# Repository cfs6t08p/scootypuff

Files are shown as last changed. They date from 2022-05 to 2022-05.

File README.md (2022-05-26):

# BOM

## OTC parts
- 1x NEMA34 stepper motor of your choice
- 1x 400mm linear rail with MGN12H carriage
- 1x Stepper motor driver ..and a way to control it TBA, in the meantime OSSM controller might work?

## 3D printed parts
- 1x Baseplate
- 1x Bearing holder
- 1x Bearing spacer (print in TPU for best fit)
- 1x Enclosure
- 1x Pinion for 14mm shaft with keyway
- 1x Rack (prints in 2 pieces)
- 1x 24mm rail thread mount
- 1x 24mm toy mount to taste

## Hardware
### Rail & attachments
- 12x 2.5x12mm wood screws
- 4x M3x12mm bolts
- 6x M3 lock nuts
- 4x M3x20mm machine screws
- 1x 5x80mm wood screw (for the Vac-u-lock adapter)

### Motor assembly
- 4x M5x30mm bolts
- 4x M5 lock nuts
- 2x M6x80mm bolts
- 2x M6 lock nuts

# How to assemble

1. Fit M3x12mm bolts with double lock nuts into the 3rd mounting hole from one side of the rail, as well as the very last mounting hole on the other side, these will act as hard stops to prevent the rail from leaving the bearing carriage
2. Attach the 24mm rail thread mount to the last two mounting holes on the end of the linear rail with two M3x12mm bolts
3. Attach the two rack pieces to the rail with 2.5x12mm wood screws, the two pieces should fit end to end, run the pinion across before tightening to ensure proper alignment
4. Mount the linear rail carriage to the bearing holder + bearing spacer with four M3x20mm machine screws, use loctite to prevent the screws from loosening with vibration
5. Mount the base plate to the front face of the motor using only two M5x30mm bolts on the bearing side, the bolts on the other side will be fitted after the enclosure is on
6. Mate the pinion to the motor shaft, the top of the pinion should be flush with the top of the shaft
7. Place the bottom part of the bearing holder into its final position on the base plate, then attach the enclosure to the top side, the parts should loosely stay in place without fastening
8. This is the perfect time to make sure the controller is working as expected, beyond this step there may be damage to the machine if the rail is driven past its limits
9. Fit the M6x80mm bolts through the top of the enclosure, the bearing holder and the baseplate
10. Fit the remaining two M5x30mm bolts through the enclosure, the base plate and the front face of the motor
11. If using the Vac-u-lock adapter, run the 5x80mm wood screw through the hole in the bottom, do not be tempted to skip this step, the plastic will crack even with moderate use!
12. This machine is incredibly powerful, be safe and make sure it can be switched off immediately if there is a problem
13. Enjoy!

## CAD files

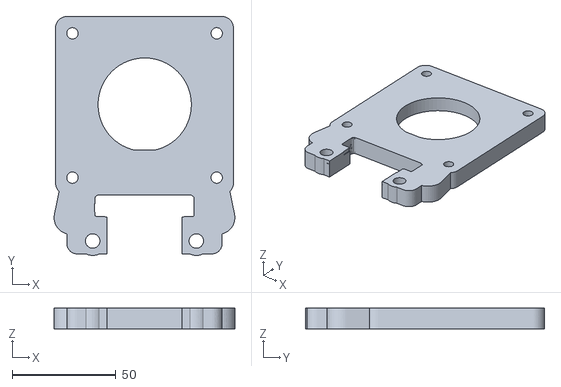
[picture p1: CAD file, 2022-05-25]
baseplate.stl
87.2 x 115.3 x 10.00

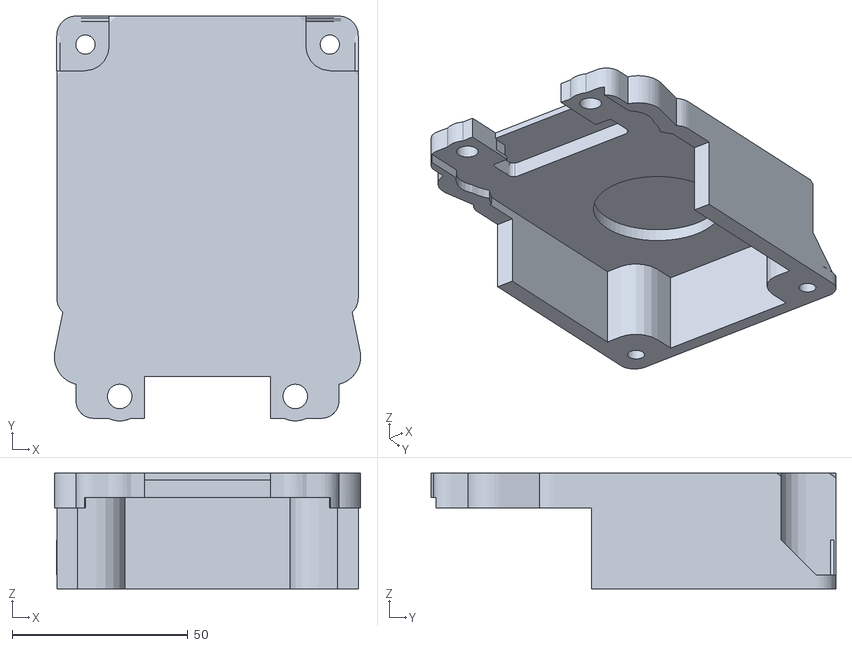
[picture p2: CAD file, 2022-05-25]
enclosure.stl
87.2 x 115.3 x 33.0

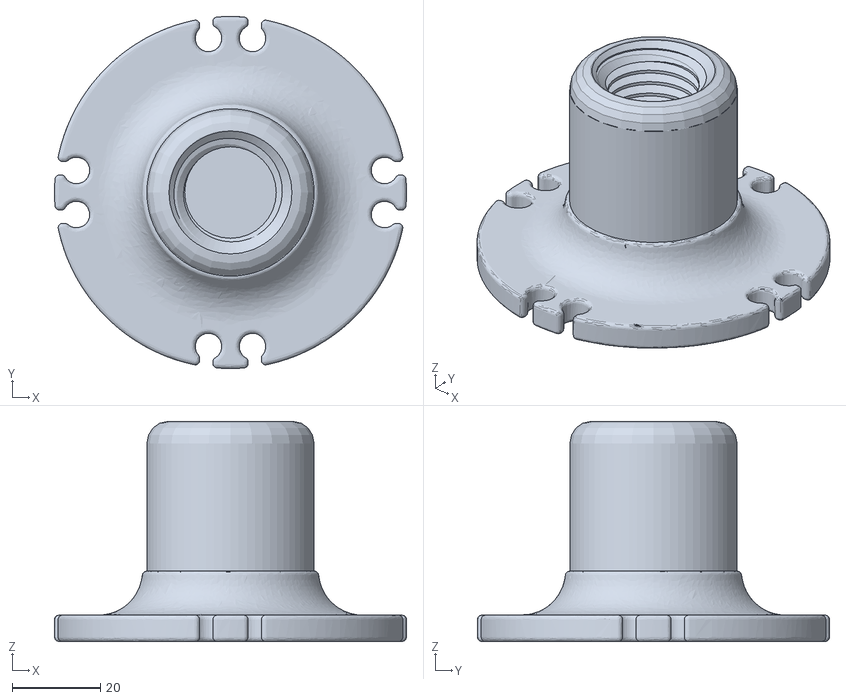
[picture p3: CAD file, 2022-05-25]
OSSM Platten - threaded 50mm.stl
80.0 x 80.0 x 50.0

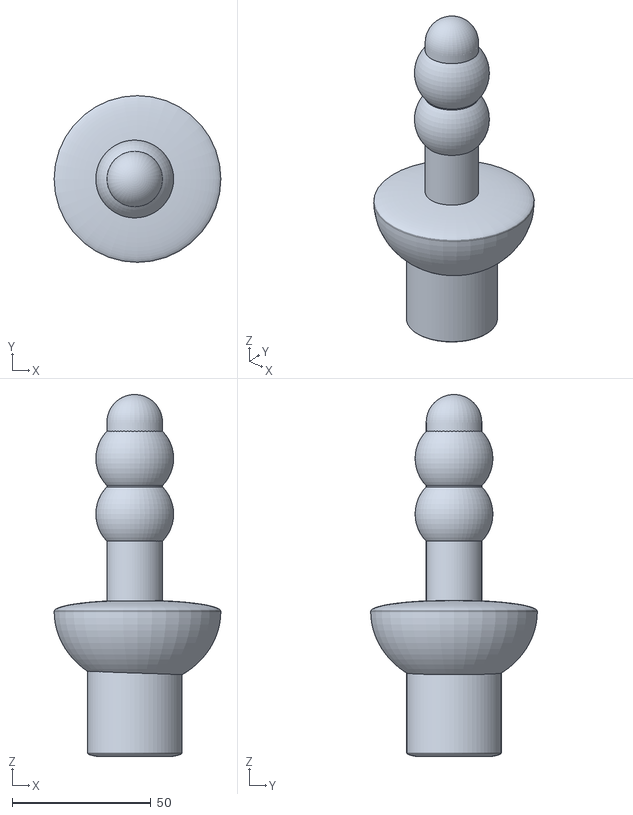
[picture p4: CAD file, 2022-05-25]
Toy mount 24mm threaded plate.stl
60.0 x 60.0 x 130.2

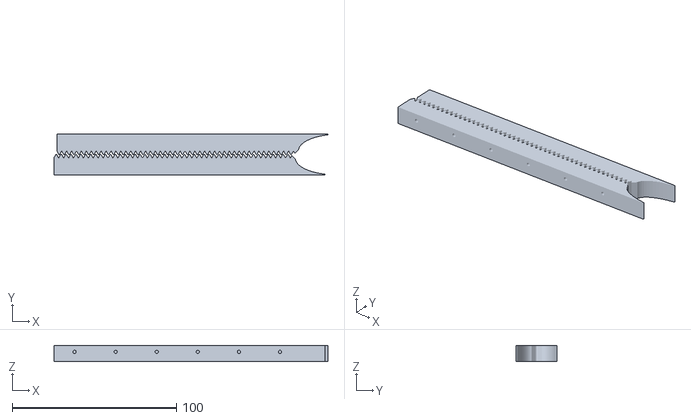
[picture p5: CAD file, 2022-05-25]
Rack_55T_pair_3mmx10x12.5.stl
166.7 x 24.8 x 10.0

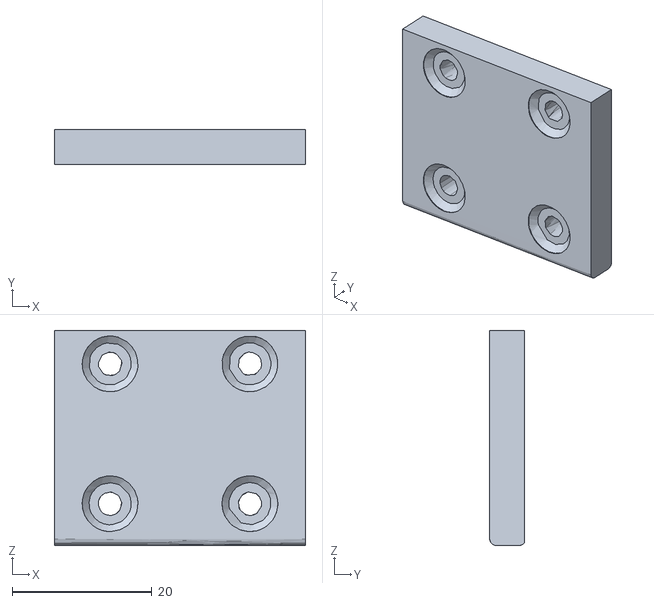
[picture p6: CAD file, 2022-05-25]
flat_bearing_spacer.stl
35.9 x 5.00 x 30.8

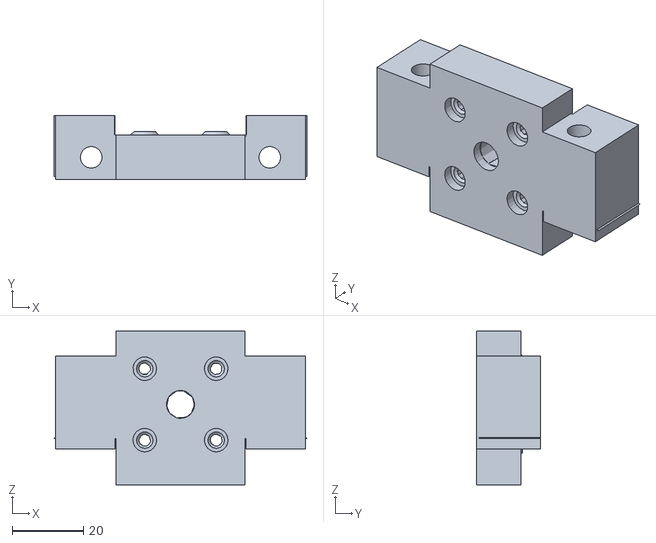
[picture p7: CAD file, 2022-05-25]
bearingholder.stl
70.8 x 17.8 x 43.0

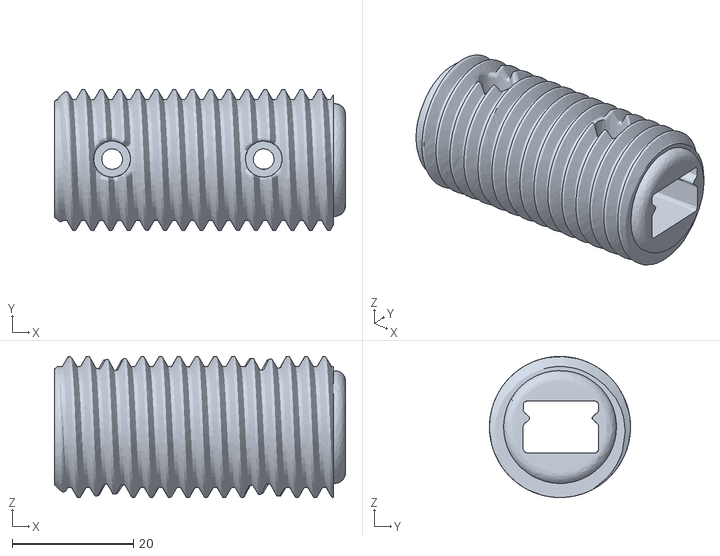
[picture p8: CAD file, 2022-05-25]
OSSM 24mm rail Thread mount M3.stl
48.0 x 23.3 x 23.3

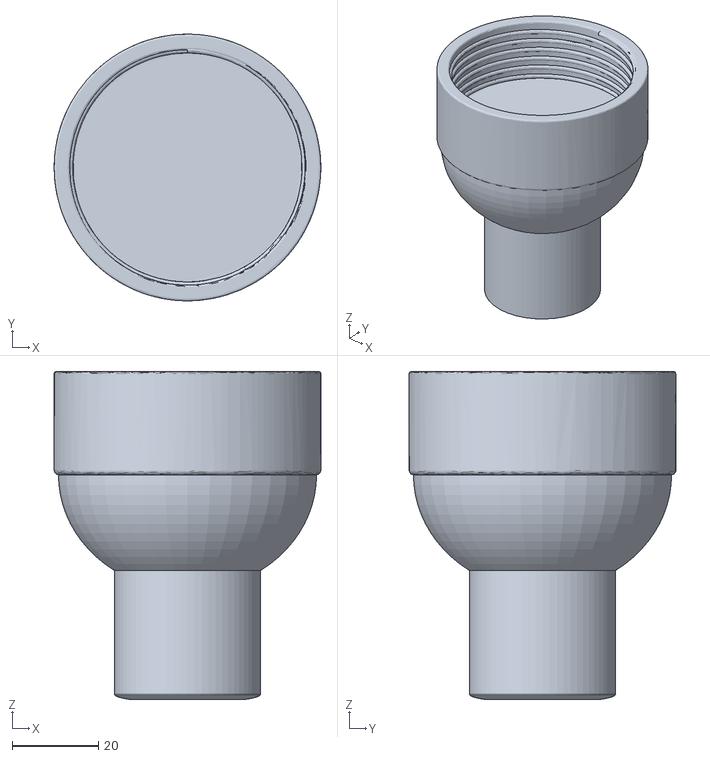
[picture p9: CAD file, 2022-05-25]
FL mount 24mm.stl
62.0 x 62.0 x 76.2

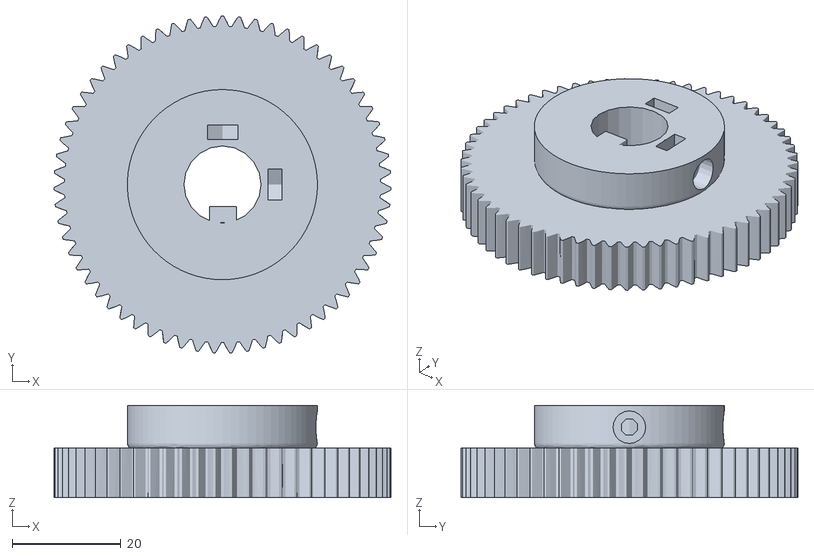
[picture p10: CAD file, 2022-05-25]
Pinion_65Tx3mmx14mm_0.80 notch.stl
62.1 x 62.0 x 16.9
